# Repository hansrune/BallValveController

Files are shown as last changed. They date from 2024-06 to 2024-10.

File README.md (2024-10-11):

# Ball Valve Controller

A DYI ball valve controller for CR05 wiring based on ESP32c3. This device is mainly intended for irrigation and main water valve automation, but is also very suitable for water leak prevention. For safety, a battery helps make sure the device returns to its default state upon reset or power failure. The device can be directly controlled to the default state by external signals such as a local water leak sensor, or you can use your home automation system to cut off water supply based on more advanced conditions.

The default state can be normally open or normally closed, and is automatically detected on restart. The safety battery voltage is also monitored and available to read remotely.

This board is tested with ESPhome and ESPEasy [firmware](#firmwares) (build instructions below), and is easily used with home automation systems that support MQTT auto discovery, the native Home Assistant API, and the many [controllers that ESPEasy supports](https://espeasy.readthedocs.io/en/latest/Controller/_Controller.html)

## Introduction

Some of the main features and benefits

- **Supports 5-wire CR05 wiring**
    - The true state of the valve can be fed back to your automation system over WiFi
    - You can detect valve malfunctioning
    - Is used by the firmware to automatically detect NO (normally open) or NC (normally closed) operation during startup
- **Supports battery backup and battery status monitoring**
    - A 9V battery is sufficient to make sure the valve returns to it's default state during power failure and resets
    - The battery voltage is readable and available as a sensor
- **Water leak sensors and protection**
    - There are inputs to force the valve to the default state as well as the activated state. Typically used with a Fibaro water leak detector associates with a Fibaro smart implant so that the valve can be "overruled" without any host controller / home automation being involved. Numerous Z-wave and Zigbee devices support this.
- **1-wire support**
    - This is used to attach DS18B20 temperature sensor. I use this with a nearby water heater. Two inputs with pull-ups are available, but you can also use multiple sensors on one wire
- **I2C support**
    - An I2C pin header with power supply is available to use with I2C sensors
    - ... or you can use the same GPIO pins for any other purpose of your choise
- **WiFi based**
    - This is almost a must have for most home automation systems
    - OTA support
    - Configuration backup, restore and bulk updates.
- **Firmware of your choise**
    - ESPEasy with Domoticz over http. Device creation uses virtual sensors
    - ESPEasy with Domotics and Home Assistant via MQTT. Device creation uses a MQTT configuration text file.
    - ESPHome to Home Assistant via MQTT and auto discovery
    - ESPHome to Domoticz via MQTT and auto discovery
    - ... and as the hardware supports using both Arduino and ESP-IF development kits, almost any other firmware can be created.
- **Seed Studio XIAO ESP32C3**
    - This device is shielded and comes with an external IPX antenna connector
    - FCC and CE regulations approved

## Setup and mounting

A typical small electic junction box is used for an easy and affordable way for housing the PCB and battery. These boxes often also support using glands for humidity protection and strain releave.

<p align="center">
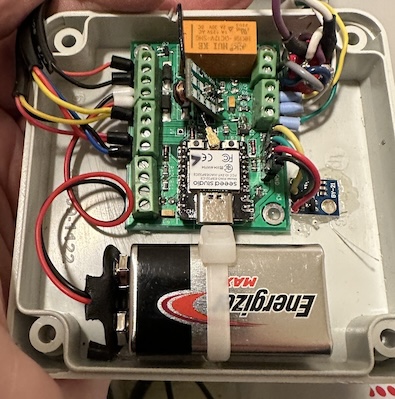
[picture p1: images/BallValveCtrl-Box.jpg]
    
</p>

Please note the positioning of the battery. The battery can be easily removed to provide room for a USB-C cable connection, in case an OTA update should fail. Failure to OTA is usually recovered by a power cycle, but bugs in OTA libaries need a physical connection for recovery.

The switch (see wiring below) is used to select between normally open and normally closed operation. As the ball valve will return to it's default position during reset, the valve position feedback switches are used to automatically determine if the setup is normally open or normally closed.

One of my permanent setups look like this:

<p align="center">
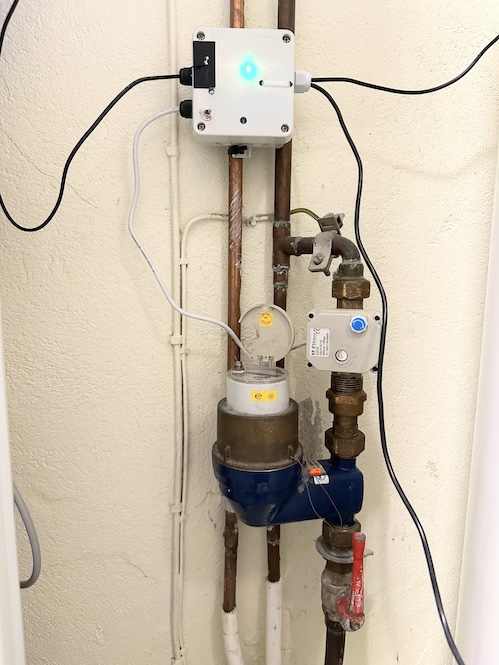
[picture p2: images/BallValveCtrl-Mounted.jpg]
    
</p>

... where the 1-wire sensors are attached to top and bottom of our electric water boiler.

## Indicators

The 5mm LEDs are suggested to be reverse mounted for the following purposes:

- LED D7 will indicate the state of valve activation - solid on or off
- LED D6
  - will blink with a duty cycle 1-4 or 4-1 to indicate valve closed or open
  - a duty cycle 1:1 will indicate a reset is ongoing
  - no change indicates out of power, device death/freeze or other

## Implementation and design

The easiest way to view the controller is probably this block level wiring diagram:

<p align="center">
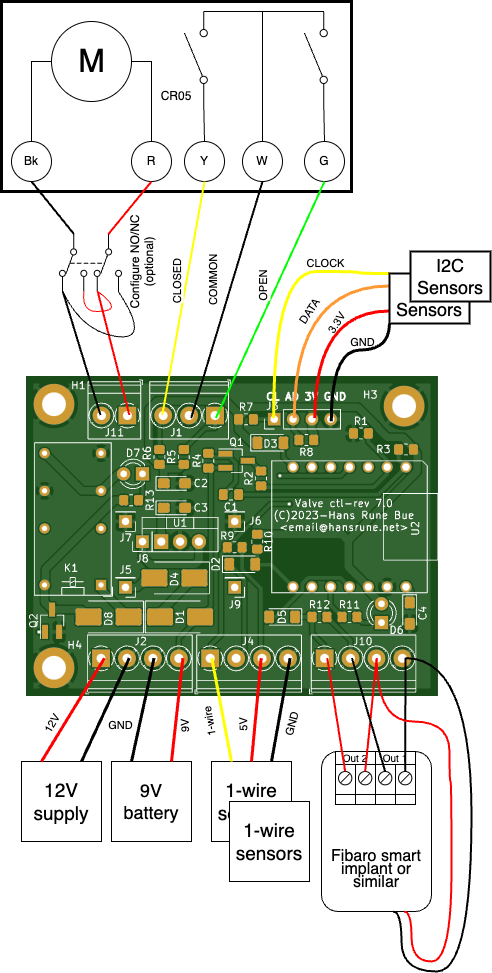
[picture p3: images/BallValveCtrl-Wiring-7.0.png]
    
</p>

This is just a typical setup for the various external components. The schematic diagram is [available here](KiCad/BallValveController-schema-7.0.pdf). The [KiCad EDA](https://www.kicad.org/) project is in the [same folder](./KiCad)

If you use more than one 1-wire sensor, it is easier in ESPHome to use both inputs (RX+TX in diagram) with automatic sensor address detection.

### GPIO pin usage

| PIN | Capabilty | Function |
|---|---|---|
| GPIO2 | Active low out | Activate battery read |
| GPIO3/A1 | Analog in | Battery read input |
| GPIO4 | Active low in | Valve open |
| GPIO5 | Active low in | Valve closed |
| GPIO6 | I2C | SDA |
| GPIO7 | I2C | SCL |
| GPIO9 | Active low out | Internal status LED |
| GPIO10 | Active high out | Valve activate to non-default state |
| GPIO20 | RX / 1-wire | Serial or 1-wire sensor |
| GPIO21 | TX / 1-wire | Serial or 1-wire sensor |

### Interfacing leak detectors

J10 is used to interface leak detectors:

| PIN  | Name | Function |
|---|---|---|
| 1 | Activate | Pull high to force non-default state  |
| 2 | Deactivate | Battery read input |
| 3 | Vcc | Supply voltage, 3.3V, 5V or 12V strap |
| 4 | GND | Ground |

#### Connecting a Fibaro Implant

A Fibaro implant may be associated with Fibaro leak detector(s). This type of device to device can work even without the Z-Wave hub being operational

- `VCC` - strap JP1 to the 12V supply as illustrated [here](#known-bugs), or just feed the Implant directly from the 12V power supply
- `Deactivate` - connect to one side of Out1 - the other side to GND
- `GND` for implant power and Out1

#### Connecting an Arduino water leak sensor

Typical Arduino water leak detectors are open collector outputs. Connect as follows:

- `VCC` - strap/solder JP1 to the 3.3V side for sensor power 
- `Deactivate` - connect to sensor output. This will force the valve to default state when activated
- `GND` - sensor power ground

## Hardware - getting started

This project uses my [KiCad-lib-ESP32 repository](https://github.com/hansrune/KiCad-lib-ESP32.git) as a [git submodule](https://www.git-scm.com/book/en/v2/Git-Tools-Submodules). To check this out, use the following:

```bash
git clone --recurse-submodules https://github.com/hansrune/BallValveController.git 
```

### Materials used

This project uses the [Seed Studio XIAO ESP32C3 RISC-V module](https://www.seeedstudio.com/Seeed-XIAO-ESP32C3-p-5431.html). This tiny device has proven to be more reliable than most ESP8266 modules used in earlier versions. This module also comes with an IPX connector for connecting an external antenna, and is delivered with a simple external antenna for good range. This device is also EMI shielded and certified.

A ball valve like [these HSH-FLO valves](https://www.ebay.com/itm/121728665101?var=420727385309) uses metal gears, and also have a manual override possibility. Despite the moderate cost, I have found them very reliable. Manufacturer claims 100k operations. I typically use a 2 or some times 3-port version, size 3/4" DN20, DC12/24V and with CR05-01 wiring, including a manual overrride whell option.

Any available 12V DC power supply delivering 1A or more should do.

There are many options and possible pinouts for DC-DC converters for the 12V to 5V conversion. A linear regulator (L7805) will need a heatsink, so a DC-DC converter is recommended.

<p align="center">
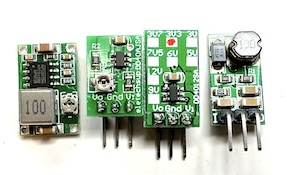
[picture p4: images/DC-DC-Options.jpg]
    
</p>

The MOSFETs need a low Vgs trigger voltage, i.e. well under 3V on full load. I have used Si2301/A1SHB for the P-channel, and Si2302/N025P for the N-channel, and 2N2222/1P - all SOT-23 packages.

Resistors are 0805 size. Screw terminals are 3.5mm, which is a tight fit when ferrules are being used.

For more information, use [this KiCad BOM](KiCad/BallValveController-BOM.csv)

## Hardware assembly

Soldering a prototype by hand is possible if you have a steady hand and a small solder iron tip. A microscope is recommended to inspect the solder joints properly.

Recommend to do the SMD parts first, then other components. I prefer to mount the 5mm LEDs on the back side.

### Hardware tests

You should test at least the following **before adding the ESP32 module**:

- Attach a battery and check that the valve can be operated both NO and NC
- Add power and check that 5V conversion is OK
- Apply 5V to the ESP32c3 pin 11 to check that the relay is operated
- Apply 0V to pin 1 of the ESP32c3 and check that pin 2 receives a 200ms readout of the battery voltage (divided by the 68k + 20k resistors)

## Firmwares

### ESPHome

ESPHome firmware can be set up from [this ESPHome configuration repository](https://github.com/hansrune/esphome-config) using the `test_ball_valve` as a template

Follow the [README](https://github.com/hansrune/esphome-config) for instructions on what you will likely want to change.

By default, MQTT auto discovery is being used. This should work out of the box with Home Assistant, Domoticz and other that support [Home Assistant MQTT Auto Discovery](https://www.home-assistant.io/integrations/mqtt/#mqtt-discovery)

In Home Assistant, the device has these controls:

<p align="center">
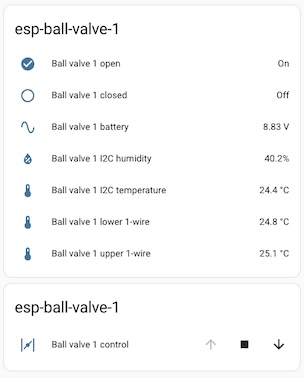
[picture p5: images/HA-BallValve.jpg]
    
</p>

... and information / diagnostics panel:

<p align="center">
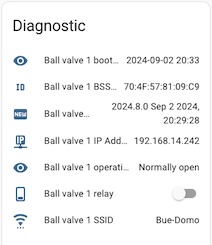
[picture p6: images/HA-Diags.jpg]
    
</p>

### ESPEasy

ESPEasy can be used with a number of different controllers / home automation systms. A custom firmware build description is [available here](https://github.com/hansrune/ESPEasy-custom/blob/builds/custom/mega-20240822-1/README-custombuilds.md)

ESPEasy requires many settings. For configuration settings and rule files, you can upload the files from [this page](./ESPEasy/) as a starting point. Please make sure to change name, unit number, controller IP addresses, NTP, syslog host and latitude/longitude. This configuration uses both a MQTT controller and a Domoticz controller. Change to what you need.

## Bugs and tweaks

### For Fibaro Smart Implants

A Fibaro Smart implant needs a 9-30V power supply. To accomodate that, you can supply 12V by running a wire on the back of the PCB as follows:

<p align="center">
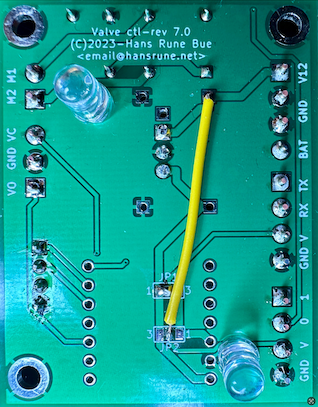
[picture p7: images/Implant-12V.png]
    
</p>

... or just connect to the 12V input terminal

<!-- 

## How to contribute

-->

## License

This project is licensed under the [GNU General Public License v3.0](GNU-LICENSE-V3.txt) for the software, [CERN-OHL-W](OHL-LICENSE.txt) for the hardware, and [CC BY-SA](CC-BY-SA-LICENCE.txt) for the documentation and ideas.

<p align="center" width="100%">
    
</p>

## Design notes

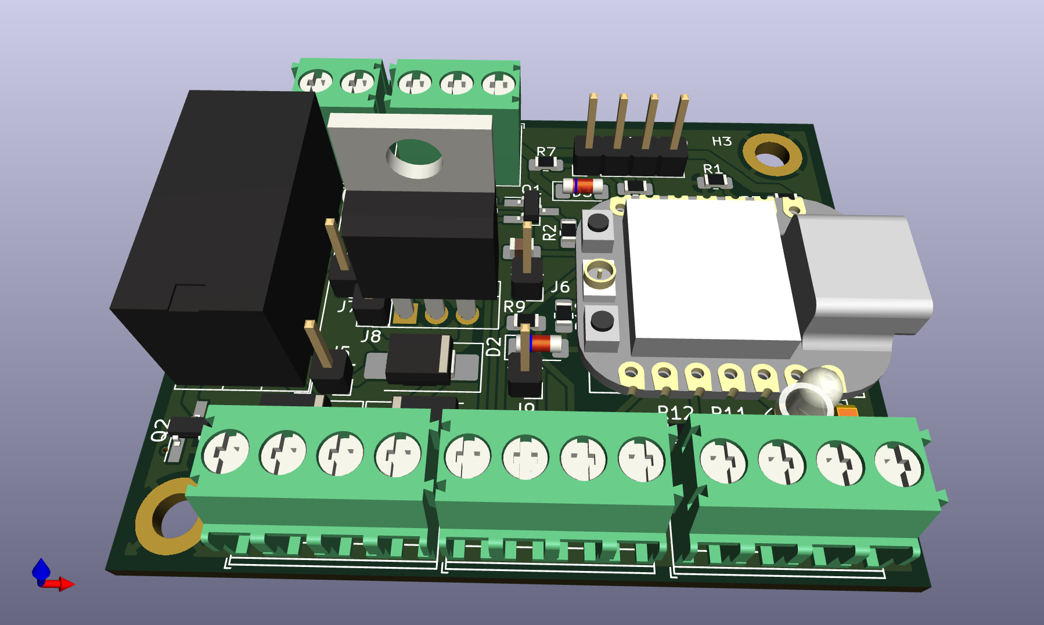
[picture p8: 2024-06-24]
images/BallValveCtrl-THT-mounts.png

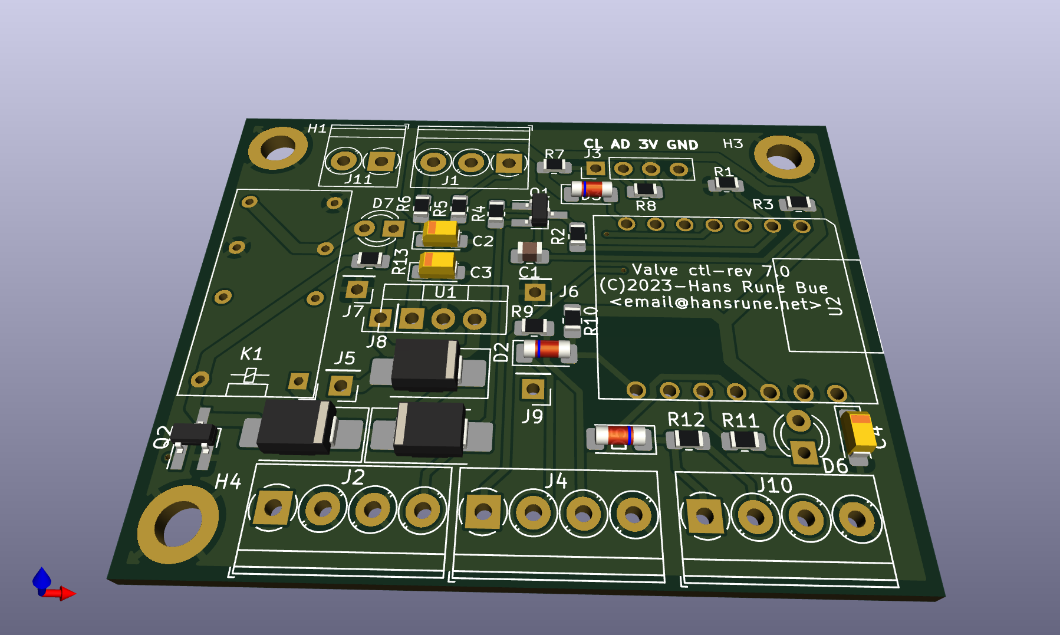
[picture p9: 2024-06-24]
images/BallValveCtrl-SMD-mounts.png

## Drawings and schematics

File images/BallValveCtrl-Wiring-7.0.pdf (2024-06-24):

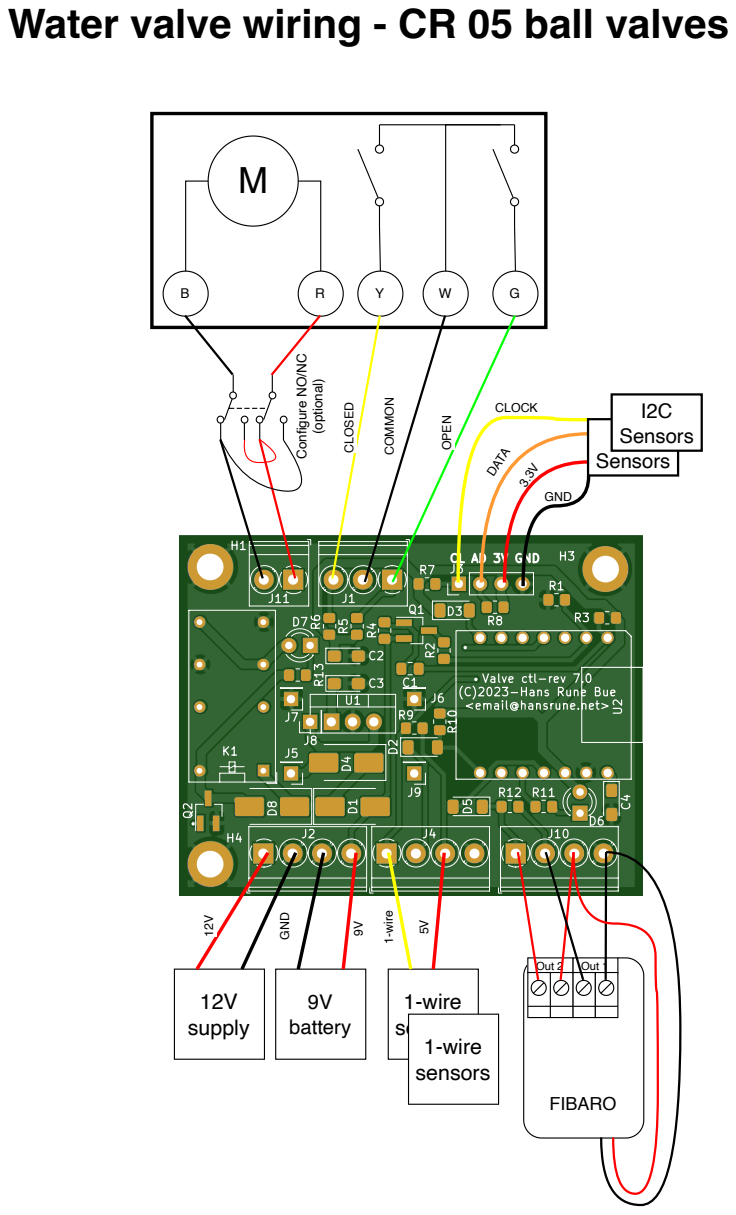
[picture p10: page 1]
G CLOSED; OPEN COMMON; FIBARO; Out 2; Out 1; 12V supply; 9V battery; GND; 1-wire; sensors ⁵V; 1-wire sensors; CLOCK; DATA; I2C Sensors

Water valve wiring - CR 05 ball valves Configure NO/NC (optional)

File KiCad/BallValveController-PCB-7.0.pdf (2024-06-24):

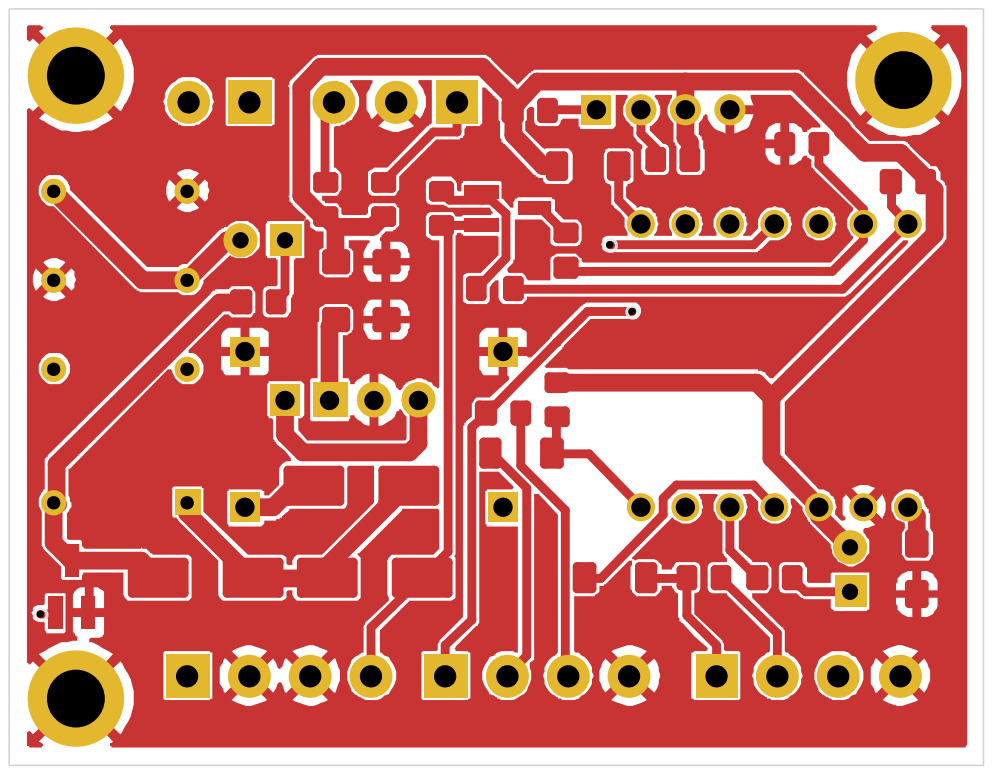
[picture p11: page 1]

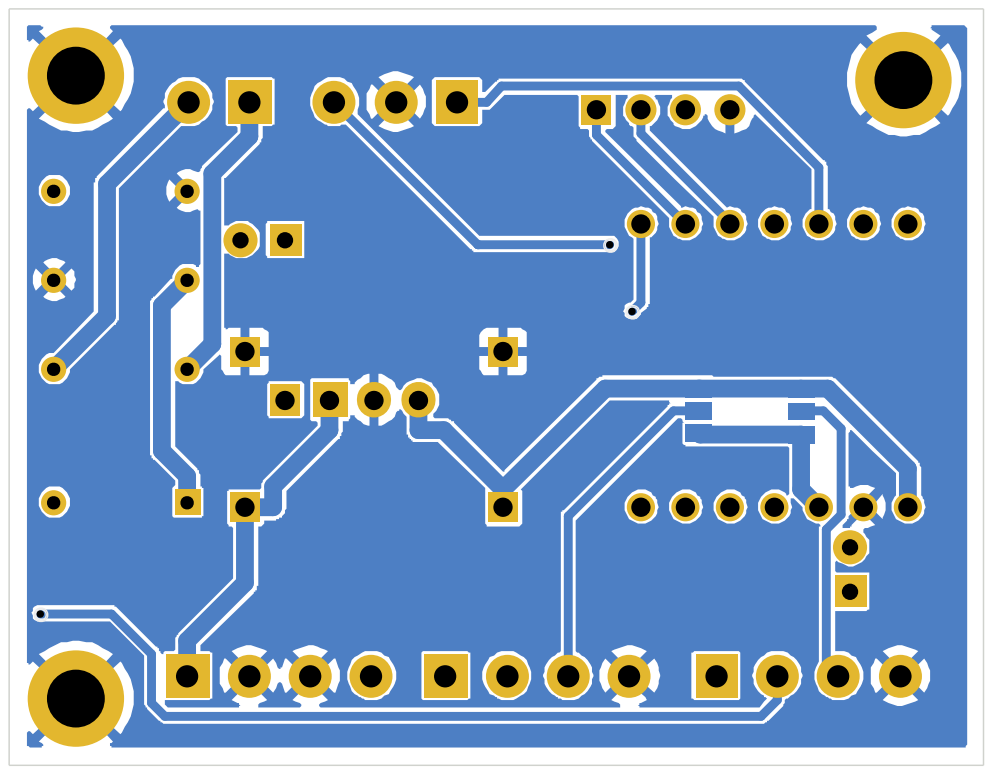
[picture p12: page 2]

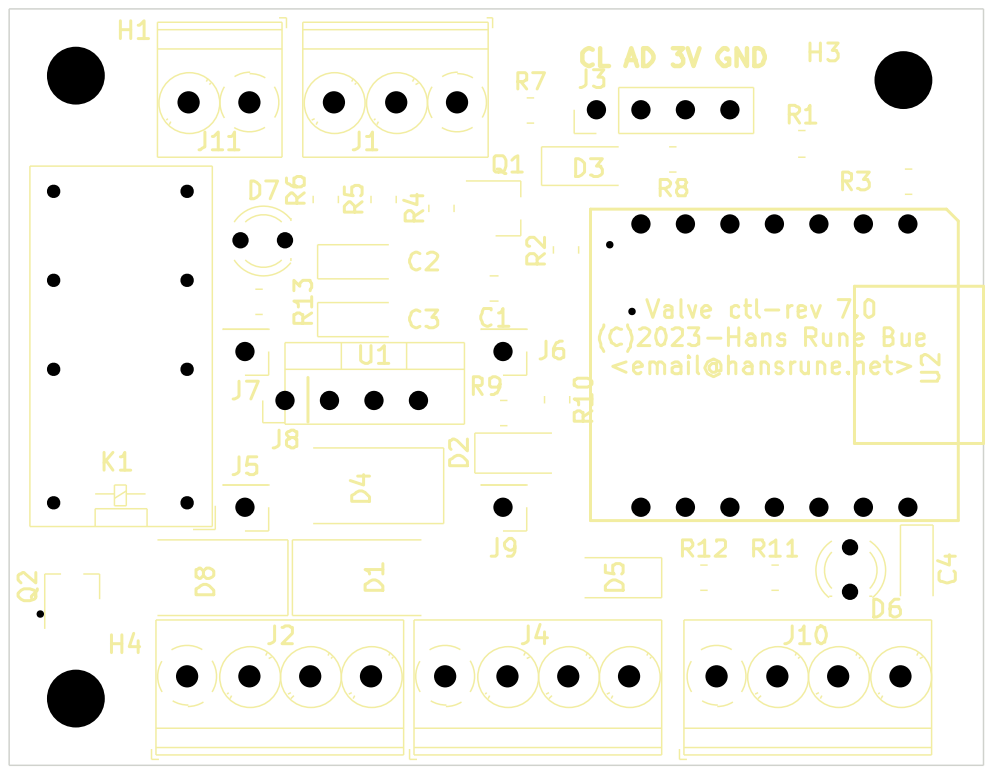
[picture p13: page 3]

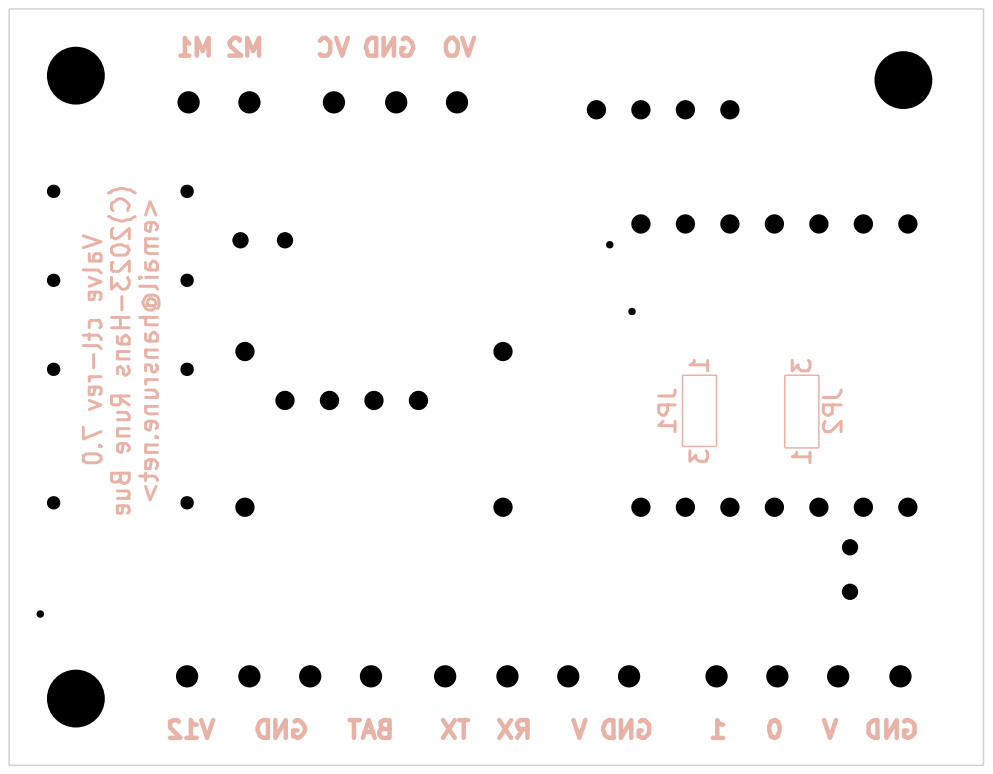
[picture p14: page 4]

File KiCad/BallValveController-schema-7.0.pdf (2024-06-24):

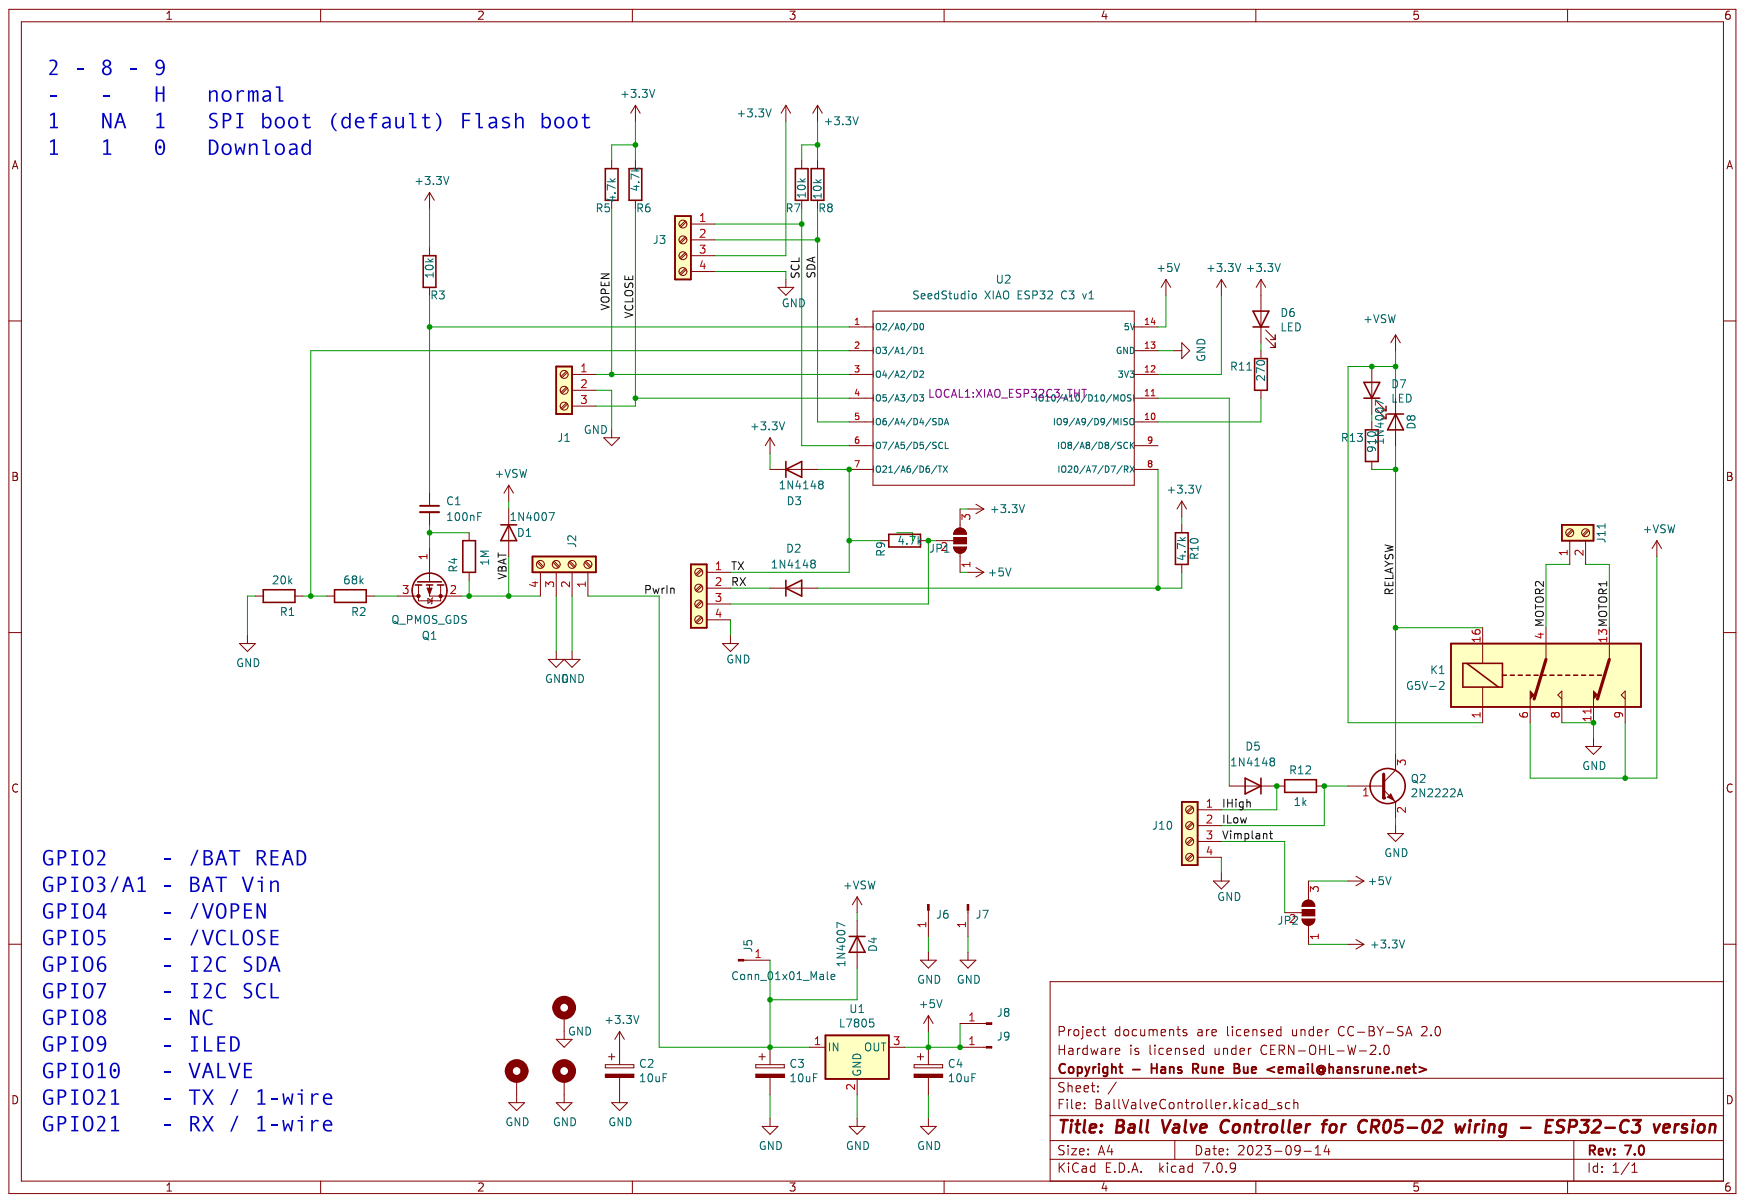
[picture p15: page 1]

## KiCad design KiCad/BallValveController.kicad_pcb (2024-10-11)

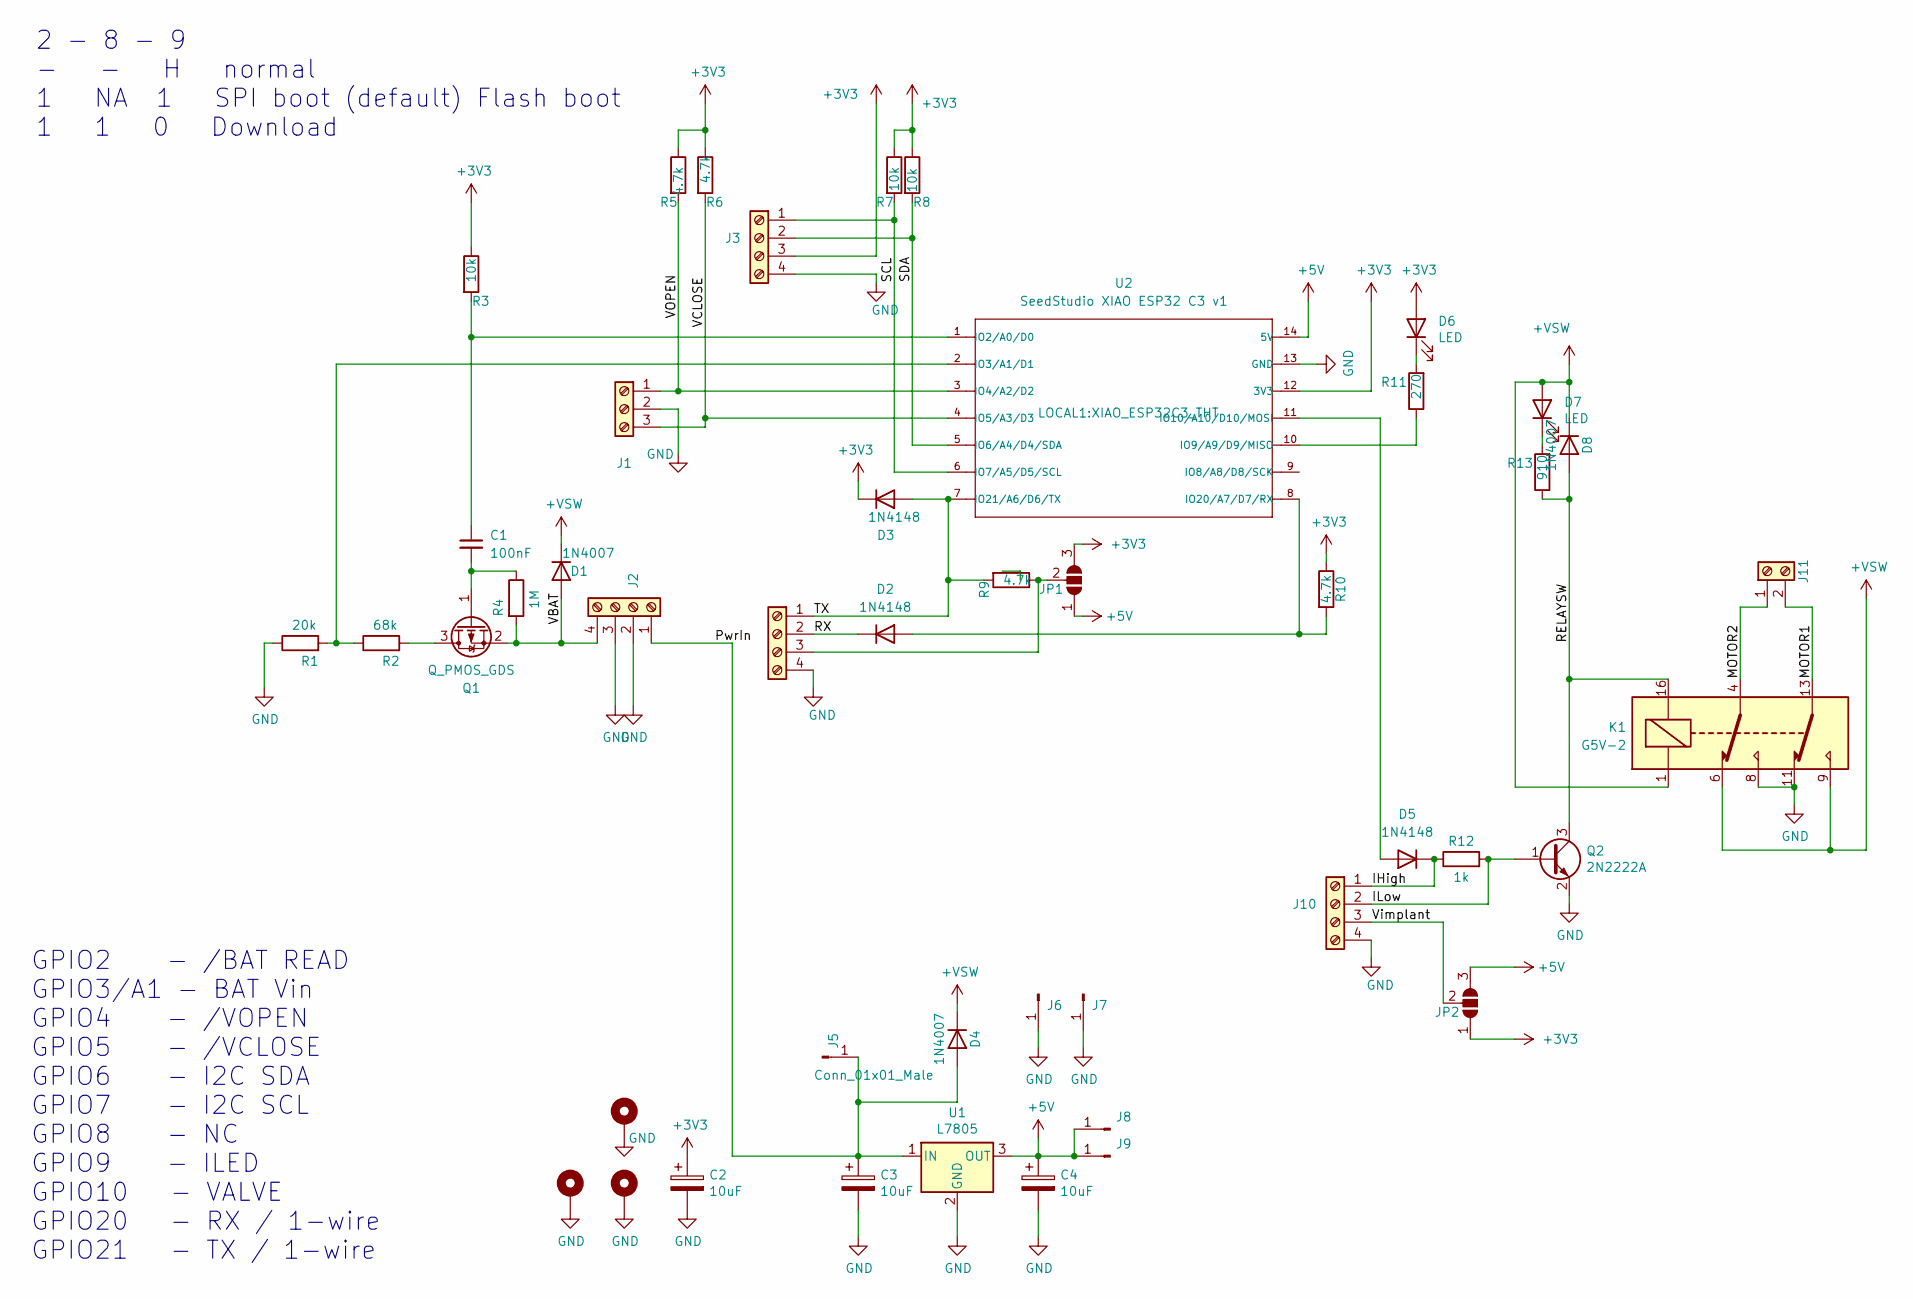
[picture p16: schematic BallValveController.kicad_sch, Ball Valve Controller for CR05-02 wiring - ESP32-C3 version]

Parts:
C1: 100nF; C_0805_2012Metric_Pad1.18x1.45mm_HandSolder
C2, C3, C4: 10uF; CP_EIA-3216-18_Kemet-A_Pad1.58x1.35mm_HandSolder
D1, D4, D8: 1N4007; D_SMB_Handsoldering
D2, D3, D5: 1N4148; D_MiniMELF
D6, D7: LED; LED_D3.0mm_Clear
H1, H3, H4: MountingHole_Pad; MountingHole_3.2mm_M3_ISO14580_Pad
J1: Screw_Terminal_01x03; TerminalBlock_Phoenix_PT-1,5-3-3.5-H_1x03_P3.50mm_Horizontal
J2, J4, J10: Screw_Terminal_01x04; TerminalBlock_Phoenix_PT-1,5-4-3.5-H_1x04_P3.50mm_Horizontal
J3: Screw_Terminal_01x04; PinHeader_1x04_P2.54mm_Vertical
J5, J6, J7, J8, J9: Conn_01x01_Male; PinHeader_1x01_P2.54mm_Vertical
J11: Screw_Terminal_01x02; TerminalBlock_Phoenix_PT-1,5-2-3.5-H_1x02_P3.50mm_Horizontal
JP1, JP2: SolderJumper_3_Open; SolderJumper-3_P1.3mm_Open_Pad1.0x1.5mm_NumberLabels
K1: G5V-2; Relay_DPDT_Omron_G5V-2
Q1: Q_PMOS_GDS; SOT-23_Handsoldering
Q2: 2N2222A; SOT-23_Handsoldering
R1: 20k; R_0805_2012Metric_Pad1.20x1.40mm_HandSolder
R2: 68k; R_0805_2012Metric_Pad1.20x1.40mm_HandSolder
R3, R7, R8: 10k; R_0805_2012Metric_Pad1.20x1.40mm_HandSolder
R4: 1M; R_0805_2012Metric_Pad1.20x1.40mm_HandSolder
R5, R6, R9, R10: 4.7k; R_0805_2012Metric_Pad1.20x1.40mm_HandSolder
R11: 270; R_0805_2012Metric_Pad1.20x1.40mm_HandSolder
R12: 1k; R_0805_2012Metric_Pad1.20x1.40mm_HandSolder
R13: 910; R_0805_2012Metric_Pad1.20x1.40mm_HandSolder
U1: L7805; TO-220-3_Vertical
U2: SeedStudio XIAO ESP32 C3 v1; XIAO_ESP32C3_THT

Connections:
+3V3: C2.1, D3.1 (K), D6.2 (A), J3.3, JP1.3 (B), JP2.1 (A), R3.1, R5.1, R6.1, R7.1, R8.1, R10.1, U2.12 (3V3)
+5V: C4.1, J8.1, J9.1, JP1.1 (A), JP2.3 (B), U1.3 (OUT), U2.14 (5V)
+VSW: D1.1 (K), D4.1 (K), D7.2 (A), D8.1 (K), K1.1, K1.6, K1.9
/IHigh: D5.1 (K), J10.1, R12.1
/ILow: J10.2, Q2.1 (B), R12.2
/MOTOR1: J11.2, K1.13
/MOTOR2: J11.1, K1.4
/PwrIn: C3.1, D4.2 (A), J2.1, J5.1, U1.1 (IN)
/RELAYSW: D8.2 (A), K1.16, Q2.3 (C), R13.1
/RX: D2.1 (K), J4.2
/SCL: J3.1, R7.2, U2.6 (IO7/A5/D5/SCL)
/SDA: J3.2, R8.2, U2.5 (IO6/A4/D4/SDA)
/TX: D3.2 (A), J4.1, R9.2, U2.7 (IO21/A6/D6/TX)
/VBAT: D1.2 (A), J2.4, Q1.2 (S), R4.2
/VCLOSE: J1.3, R6.2, U2.4 (IO5/A3/D3)
/VOPEN: J1.1, R5.2, U2.3 (IO4/A2/D2)
/Vimplant: J10.3, JP2.2 (C)
GND: C2.2, C3.2, C4.2, H1.1, H3.1, H4.1, J1.2, J2.2, J2.3, J3.4, J4.4, J6.1, J7.1, J10.4, K1.8, K1.11, Q2.2 (E), R1.1, U1.2 (GND), U2.13 (GND)
unnamed: D2.2 (A), R10.2, U2.8 (IO20/A7/D7/RX)
unnamed: D5.2 (A), U2.11 (IO10/A10/D10/MOSI)
unnamed: D6.1 (K), R11.2
unnamed: D7.1 (K), R13.2
unnamed: J4.3, JP1.2 (C), R9.1
unnamed: Q1.3 (D), R2.2
unnamed: C1.2, Q1.1 (G), R4.1
unnamed: C1.1, R3.2, U2.1 (IO2/A0/D0)
unnamed: R1.2, R2.1, U2.2 (IO3/A1/D1)
unnamed: R11.1, U2.10 (IO9/A9/D9/MISO)

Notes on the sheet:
2 - 8 - 9 - - H normal 1 NA 1 SPI boot (default) Flash boot 1 1 0 Download
GPIO2 - /BAT READ GPIO3/A1 - BAT Vin GPIO4 - /VOPEN GPIO5 - /VCLOSE GPIO6 - I2C SDA GPIO7 - I2C SCL GPIO8 - NC GPIO9 - ILED GPIO10 - VALVE GPIO20 - RX / 1-wire GPIO21 - TX / 1-wire

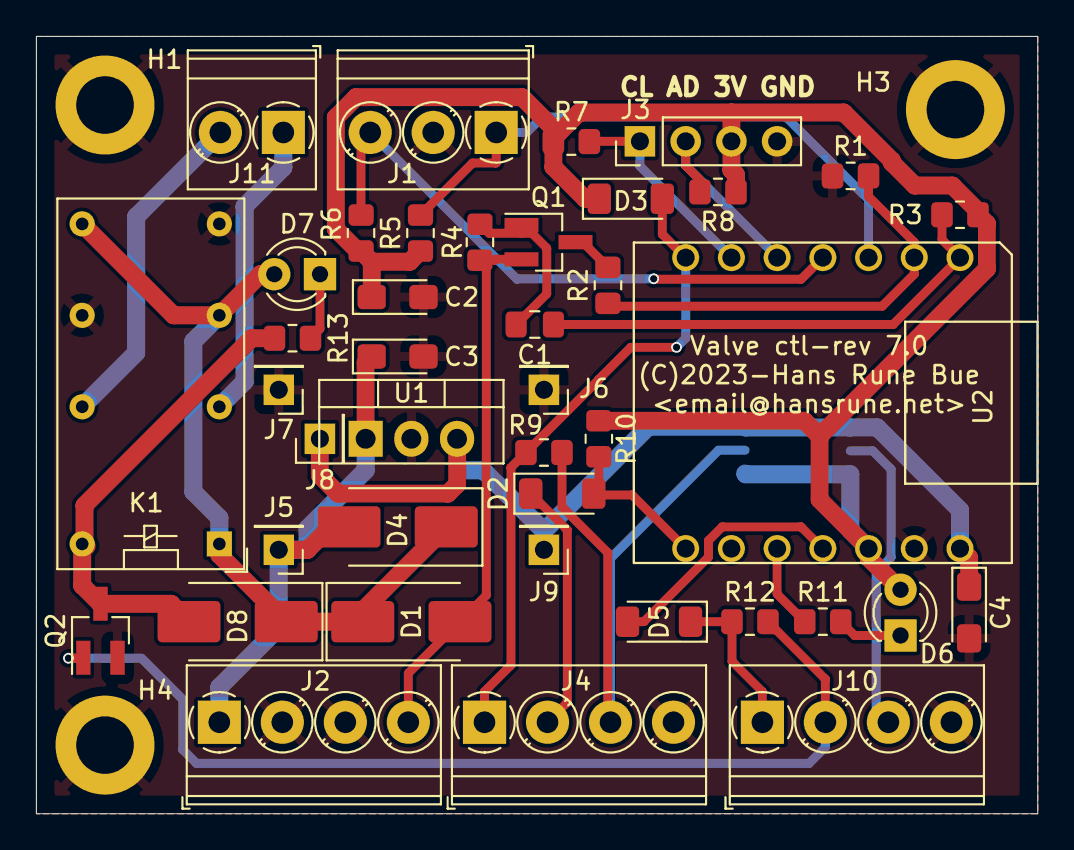
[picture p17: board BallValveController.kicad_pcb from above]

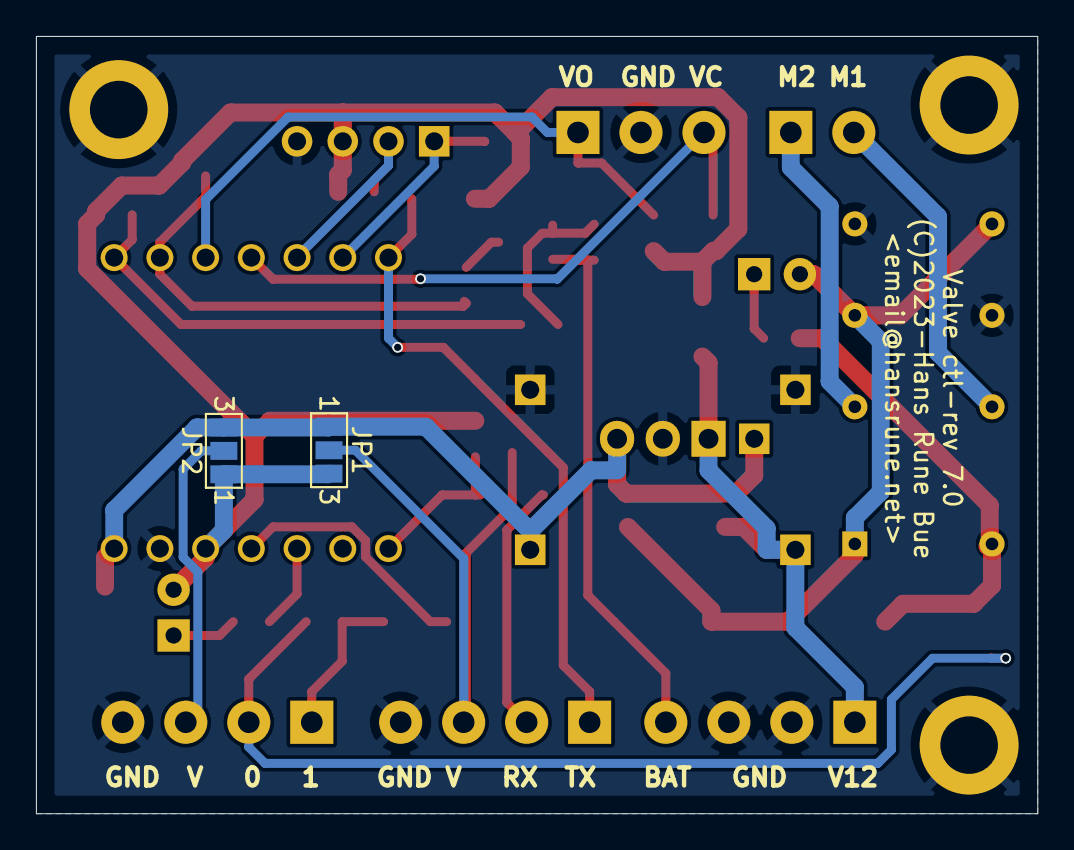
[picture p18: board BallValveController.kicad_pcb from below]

Board: 2 copper layers, 55.6 x 43.2 mm, 46 parts (2 on the bottom side), 28 nets.

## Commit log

2024-06-24 Added KiCad files and KiCad images
    [BallValveController.kicad_pcb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]
2024-06-24 v7.0.1 - updated metadata only
    [BallValveController.kicad_pcb, BallValveController.kicad_sch]
2024-09-19 New 3D model
    [BallValveController.kicad_pcb]

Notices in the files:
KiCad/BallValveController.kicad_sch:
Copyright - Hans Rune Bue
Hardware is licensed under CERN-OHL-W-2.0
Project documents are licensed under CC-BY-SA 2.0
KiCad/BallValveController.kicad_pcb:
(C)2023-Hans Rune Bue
